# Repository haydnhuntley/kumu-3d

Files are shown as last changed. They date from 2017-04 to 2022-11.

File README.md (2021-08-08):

# kumu-3d

## The Kumu-3D Printer

### *Kumu* means *teacher* in the Hawaiian language.

I wish to thank Johann C. Rocholl for his groundbreaking work on the Rostock and Kossel 3D Printers. This design was derived from his work and that of many other innovators.

The Kumu-3D is a Delta printer improving on the [Kossel Plus](http://www.kosselplus.com "Kossel Plus"), which I designed to extend and improve on Johann's original [Kossel](http://reprap.org/wiki/Kossel "Kossel").

The Kumu-3D's features are:

* 300mm diameter borosilicate build plate, yielding a build area over 250mm in diameter.
* 250mm diameter 24V 250W silicone heater.
* 24v power supply, to give the motors twice as much power for faster acceleration and more precise positioning.
* E3D-style hotend.
* 32-bit Smoothieware controller from AZSMZ, with LCD display.
* Carbon fiber, magnetic, zero-backlash arms.
* 0.9&deg; motors, 1/32 stepping, 16-tooth pulleys yield 400 steps/mm with a worst case real world resolution of 20&micro;m and an average resolution of about one-third of that.
* Dampers for near silent operation.
* 2020 extrusions with diagonal bracing for increased stiffness.
* flying extruder for better retraction performance.
* optional 9mm GT2 belts for increased precision.
* Integrated spool holder with bearings on top.
* Build cost around $600 in quantity one, including US shipping.
* With the standard 750mm vertical extrusions and 304mm arms, it yields a maximum Z of 290mm and maximum diameter of 260mm.  With 1000mm vertical extrusions and 360mm arms, it should yield a build height of over 500mm and diameter up to 300mm.

Here is the GoogleDocs spreadsheet containing the [Bill of Materials](https://docs.google.com/spreadsheets/d/1ovnhxit7gjctnHXA3ArEihpogoxfmhG4zKcSKq6PfBs/edit?usp=sharing). 
Here is a list of the fasteners required and where they are used: [Fasteners](https://docs.google.com/spreadsheets/d/1ovnhxit7gjctnHXA3ArEihpogoxfmhG4zKcSKq6PfBs/edit#gid=828928504)

Note: this is no longer a *Work-in-Progress* -- nine Kumu-3D's have been built and are printing, and two more are on the way!  I'm in the process of writing up how to build them, which is at:  [Assembly Instructions](https://docs.google.com/document/d/1tWf-NENtzvH9kXuD4_r2AeAENZi3MvYkmVscPsnDQXc/edit?usp=sharing)

This isn't an average printer, it is an **extraordinary** one.

I've switched to using dual-drive, geared ("BMG" style) extruders. They have triple the torque, and double the filament grip.
I've been using $15 ones from DotBit, but there are many decent brands: https://www.aliexpress.com/item/4000419512195.html

Here is a link to the AZSMZ's LCD display holder (designed by Rick Yang):  [
LCD mount for AZSMZ 12864 with TF slot](http://www.thingiverse.com/thing:1610241)

Here are some photos of Kumu-3D#1:
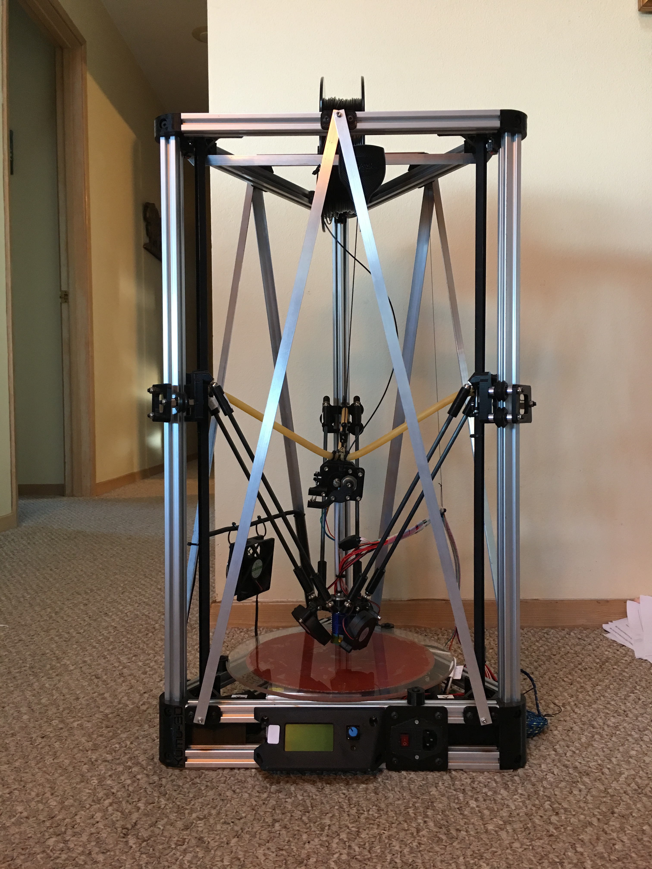
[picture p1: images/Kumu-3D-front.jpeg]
Kumu-3D Front Kumu-3D Front

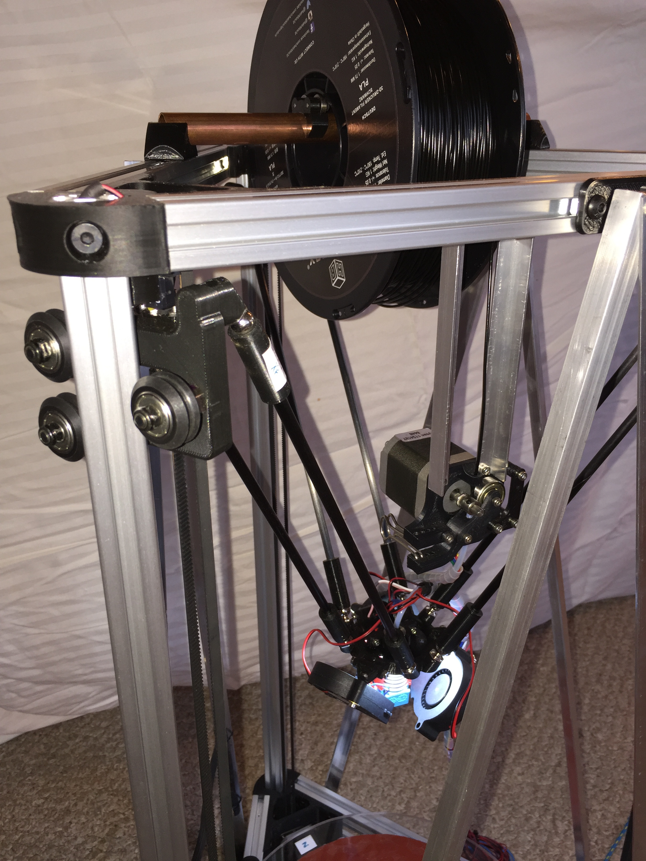
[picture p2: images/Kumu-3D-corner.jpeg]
Kumu-3D Corner Kumu-3D Corner

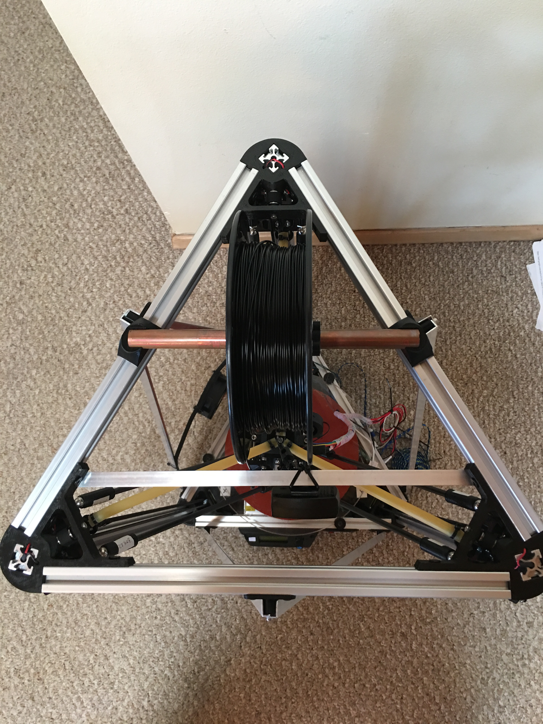
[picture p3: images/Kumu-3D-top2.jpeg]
Kumu-3D Top Kumu-3D Top

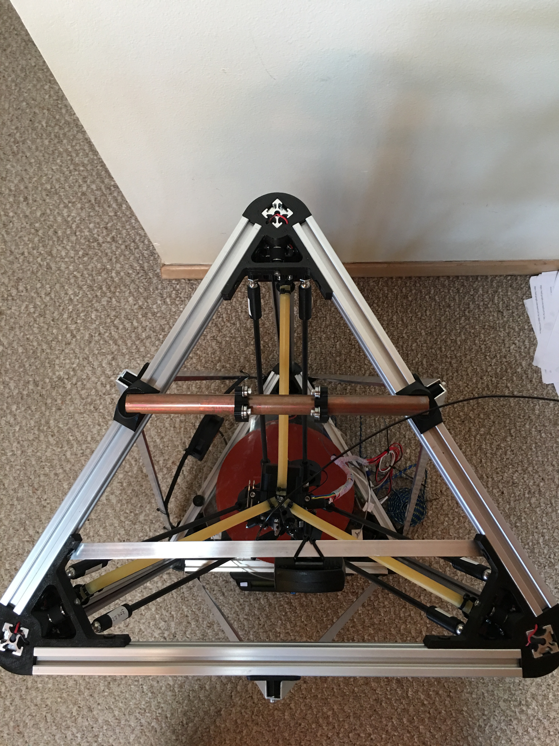
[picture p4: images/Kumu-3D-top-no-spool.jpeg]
Kumu-3D Top (no spool)


Here are some photos of a 3DBenchy torture test printed in PLA at 60mm/sec:
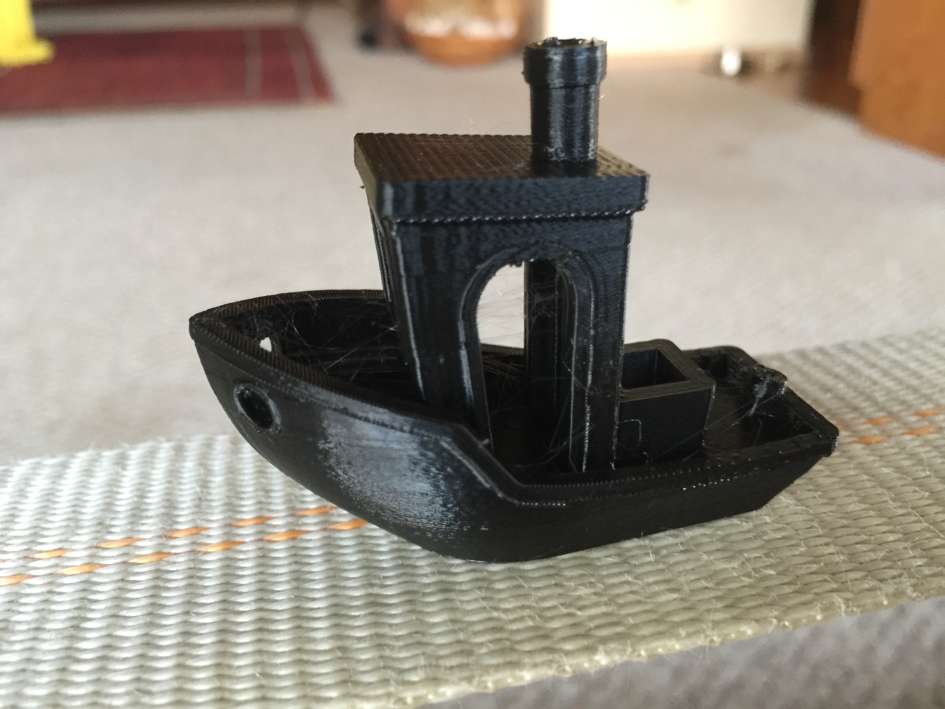
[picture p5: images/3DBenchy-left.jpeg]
3DBenchy Left 3DBenchy Left

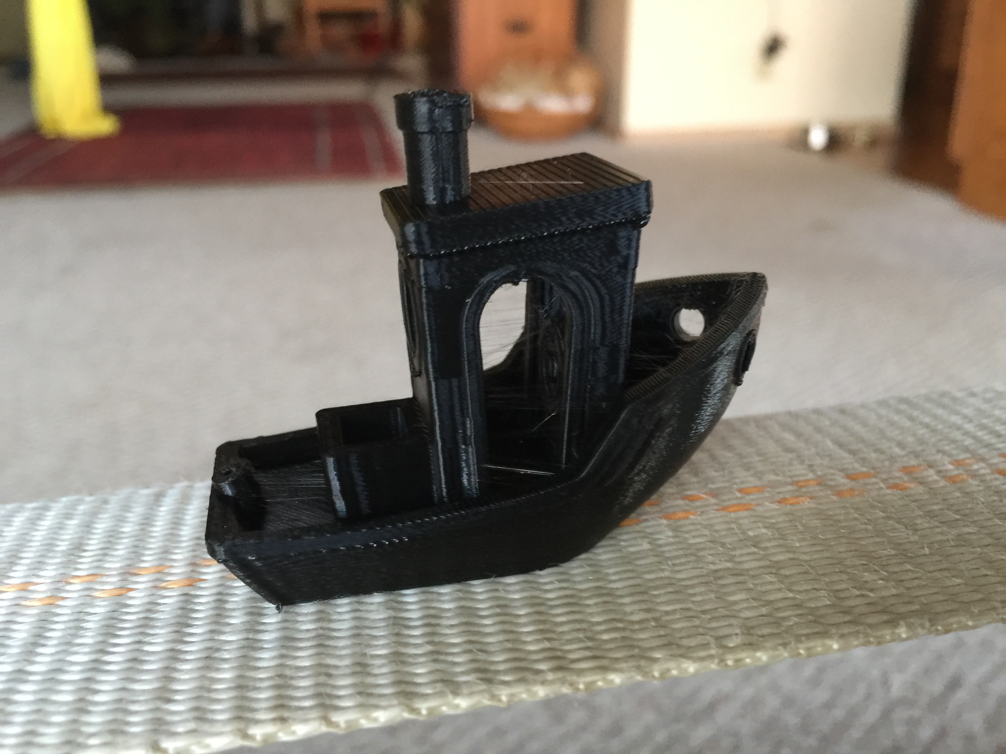
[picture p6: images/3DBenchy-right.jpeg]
3DBenchy Right

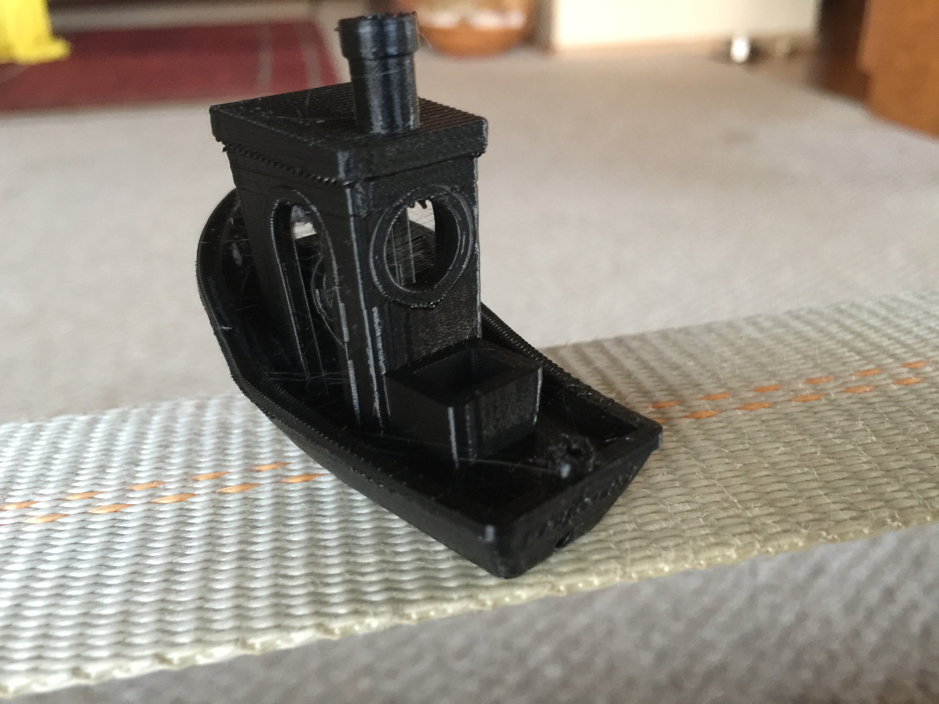
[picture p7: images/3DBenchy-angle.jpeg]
3DBenchy Angle

There is a little bit of very fine stringing, so I'll need to increase the retraction or lower the temperature.
(These were printed before switching to using the flying extruder.)
Note how nicely it handled the overhangs.

<!---
Some useful links for Markdown language:
 * [Adam's Markdown Cheatsheet](https://github.com/adam-p/markdown-here/wiki/Markdown-Cheatsheet)
 * [Laura's Markdown Cheatsheet](https://github.com/tchapi/markdown-cheatsheet/blob/master/README.md)
 * [Markdown Syntax Guide](https://confluence.atlassian.com/bitbucketserver/markdown-syntax-guide-776639995.html)
--->

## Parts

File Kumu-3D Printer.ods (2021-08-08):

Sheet: Non-printed parts
Cost | Quantity | Where Used | Description | Subtotal | Part Number | Source | Alternative Source
$20.00 | 1 | frame | 2020 aluminum extrusions | $20.00 | 2020KXL-Silver | http://www.robotdigg.com/product/494/2020-aluminum-extrusion-for-Kossel-XL
$7.64 | 3 | A-bracing, extruder mount | 8' pieces of 1/2" aluminum L-channel | $22.92 |  | http://www.homedepot.com/p/Everbilt-1-2-in-x-96-in-Aluminum-Angle-Bar-with-1-20-in-Thick-802677/204273980
$0.90 | 12 | carriages | eccentric spacers | $10.80 | PXZhu | http://www.robotdigg.com/product/626/Openbuilds-decentration-post
$1.49 | 6 | misc | packs of 10 M5x10 black steel low profile screws | $8.94 | 878 - pack | http://openbuildspartstore.com/low-profile-screws-m5/
$1.80 | 1 | misc | packs of 50 M5x8 black steel button head socket cap screws | $1.80 | BSCS-M5*8_50 | http://www.robotdigg.com/product/706/M3-or-M5-Button-Socket-Cap-Screw
$7.50 | 1 | misc | pack of 100 M5 pre-assembly T-nuts | $7.50 | PreNut20-M5 | http://www.robotdigg.com/product/317/Pre-assembly-T-nuts-for-2020-aluminum-profile
$84.00 | 1 | controller | AZSMZ 32bit controller, 12864 LCD, 5 x DRV8825 | $84.00 |  | http://www.ebay.com/itm/New-Ver-2-1-AZSMZ-32bit-controller-AZSMZ-12864-LCD-4-x-DRV8825-/262633912155
$6.75 | 1 | controller | 4GB or larger micro SD card | $6.75 |  | https://www.amazon.com/SanDisk-microSD-High-Capacity-microSDHC/dp/B00488G6P8
$9.00 | 1 | wiring | wiring harness | $9.00 |  | http://www.ebay.com/itm/171207706681
$21.96 | 1 | power | 24V 15A power supply | $21.96 |  | https://www.amazon.com/EAGWELL-Universal-Regulated-Switching-Computer/dp/B01IOK5FM0/
$1.00 | 1 | power | fuse holder/power switch/power cord socket | $1.00 | AC250-01A-Ear Screw Hole | http://www.robotdigg.com/product/744/AC-rocker-switch-power-inlet-socket-w/-fuse
$7.00 | 4 | stepper motors | NEMA17 0.9° stepper motors | $28.00 | 42HM48-1684 | https://www.robotdigg.com/product/1250/0.9-step-angle-NEMA17-stepper-motors
$2.20 | 3 | motor mounts | NEMA17 motor dampers | $6.60 | 17DAMPER | http://www.robotdigg.com/product/341/Antivibration-damper-4-nema17-stepper
$9.95 | 1 | hotend | E3D-style hotend, 24V, Bowden, 1.75mm | $9.95 | w/fan+PTFE tube, voltage: 24v, nozzle: 0.4mm/1.75mm | https://www.ebay.com/itm/All-Metal-Extruder-Hotend-Bowden-J-head-V6-For-Makerbot-Reprap-3D-printer-parts/132335314415 | https://www.filastruder.com/products/lite6?variant=1283850628
$14.99 | 1 | extruder | BMG-stle dual-drive, geared extruder | $14.99 |  | https://www.aliexpress.com/item/4000419512195.html
$5.00 | 1 | top corners (6), spool holder (4) | 10 pack of F623ZZ flanged bearings | $5.00 | F623ZZ | http://www.robotdigg.com/product/132/Flanged-Ball-Bearing-F623ZZ
$2.50 | 1 | top corners (3) | 10 pack of 623ZZ bearings | $2.50 | 623ZZ | https://www.robotdigg.com/product/62/623ZZ-Ball-Bearing
$0.60 | 1 | extruder | 608ZZ extruder bearing | $0.60 | S608ZZ | http://www.robotdigg.com/product/980/440C-SUS-Ball-Bearing-S608ZZ,-SF608ZZ
$1.80 | 12 | carriages | Delrin W-wheels | $21.60 | DelrinVSB | http://www.robotdigg.com/product/521/Delrin-or-SUS-Via-S-Bearing
$0.40 | 4 | limit switches | micro switches | $1.60 | SS-5GL0 | http://www.robotdigg.com/product/398/Pin-Plunger-Switch-Endstop
$20.99 | 1 | carriages | 5 meters of GT2 belt, 9mm wide | $20.99 |  | https://www.ebay.com/itm/GT2-2GT-open-Synchronous-Timing-Belt-Width-6-9-15mm-Small-Backlash-3D-Printer-/221884227725 | eBay: powge
$9.89 | 1 | carriages | pack of 5 GT2 16-tooth pulleys, 10mm wide, 5mm bore | $9.89 |  | https://www.ebay.com/itm/253544544720
$14.00 | 1 | bed | borosilicate glass bed, 300mm diameter, 5mm thick | $14.00 | Gls300-D300-5 Round | http://www.robotdigg.com/product/490/300mm-Borosilicate-Glass-for-3D-Printing
$18.00 | 1 | bed | silicone heater, 24v, 250mm diameter | $18.00 | SRht250-24VDC_Round | http://www.robotdigg.com/product/117/250mm-or-270mm-Silicone-Rubber-Heater-Pad
$113.00 | 1 | misc | RobotDigg.com express shipping | $113.00
$13.90 | 1 | tools | set of metric ball nose allen wrenches | $13.90 |  | https://www.amazon.com/gp/product/B0006O4ADI/
$39.95 | 1 | tools | 0-150mm calipers (optional but very useful) |  |  | https://www.amazon.com/Composite-Vernier-Digital-70019-Millimeters/dp/B01BEE86II
$2.97 | 1 | printing | glue stick, large (any brand is OK) | $2.97 |  | https://www.walmart.com/ip/Elmer-s-Large-School-Glue-Stick-22g-3pk/17011268
$22.98 | 1 | printing | kg of 1.75mm PLA filament | $22.98 |  | http://www.amazon.com/Hatchbox-1-75mm-3D-Printer-Filament/dp/B00J0ECR5I
 |  |  | Total | $475.29

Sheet: Fasteners
 | Counts | Upper Frame | Lower Frame | Vertical Extrusions | A-Bracing | Carriages | Effector | AZSMZ Holder | LCD Display Holder | Power Supply Holders | Fuse Plug Holder | Extruder | Flying Extruder Suspender | Copper Pipe Spool Holder | Copper Pipe Bearing Holder | Glass Holders
M5x50 | 12 |  |  |  |  | 12
M5x20 | 5 |  |  |  |  |  |  |  | 2 |  |  |  |  |  |  | 3
M5x10 | 54 | 12 | 24 | 18
M5x8 | 30 |  |  |  | 18 |  |  | 2 |  | 4 | 4 |  |  | 2
M5 pre-install nut | 89 | 12 | 24 | 18 | 18 |  |  | 2 | 2 | 4 | 4 |  |  | 2 |  | 3
M5 nylock nut | 12 |  |  |  |  | 12
M5 washer | 4 |  |  |  |  |  |  |  |  |  |  |  |  |  | 4
M3x35 | 9 |  |  |  |  | 9
M3x25 | 9 | 3 |  |  |  |  | 3 |  |  |  |  | 3
M3x20 | 8 |  |  |  |  |  | 5 |  |  |  |  | 1 | 2
M3x10 | 19 |  |  |  | 9 | 3 |  |  |  |  |  | 2 | 1 |  | 4
M3x8 | 12 |  | 6 |  |  |  |  | 4 |  |  |  | 2
M3x6 | 18 |  | 6 |  |  |  | 2 |  | 4 | 4 | 2
M3x4 | 2 |  |  |  |  |  |  |  |  |  | 2
M3 nut | 21 |  |  |  |  | 9 | 8 |  |  |  |  | 2 | 2
M3 nylock nut | 16 |  |  |  |  | 9 | 6 |  |  |  |  |  | 1
M3 washer | 10 | 3 |  |  |  |  | 3 |  |  | 4
M2.5x12 | 8 | 6 |  |  |  |  | 2

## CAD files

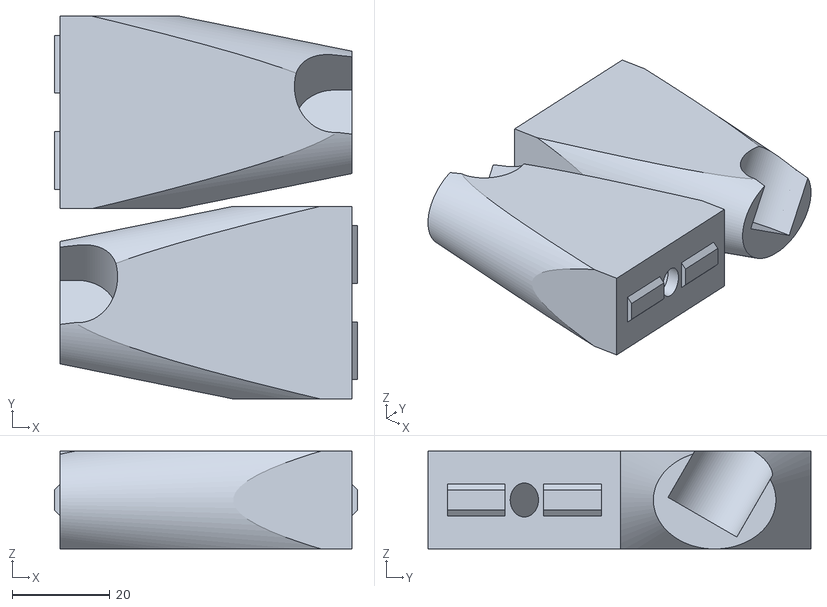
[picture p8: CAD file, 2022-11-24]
copperPipeSpoolHolder.stl
62.2 x 78.5 x 20.0

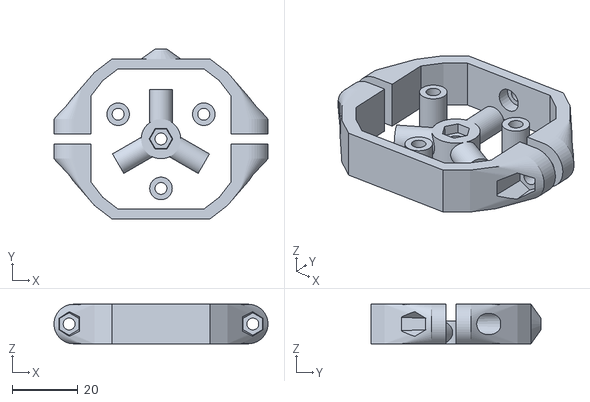
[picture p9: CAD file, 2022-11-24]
flyingExtruderSuspender.stl
64.9 x 51.5 x 12.0

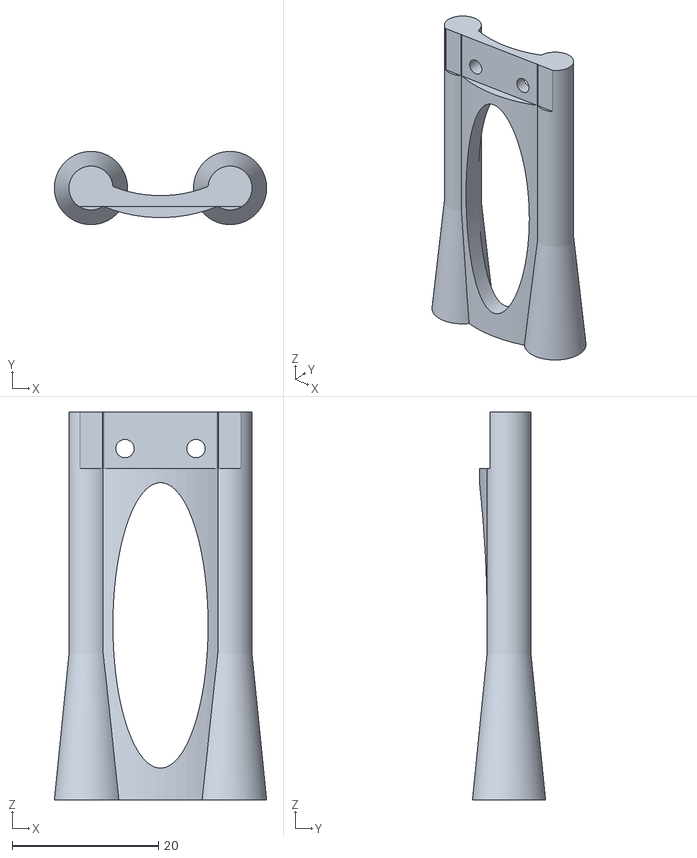
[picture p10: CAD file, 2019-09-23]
zProbe.stl
29.0 x 10.0 x 53.0

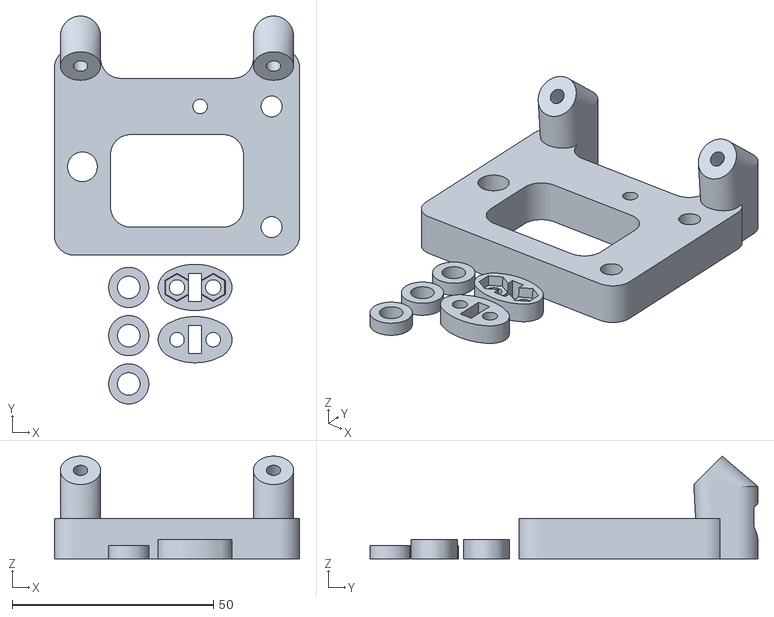
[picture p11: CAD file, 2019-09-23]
carriage.stl
61.0 x 96.5 x 25.6

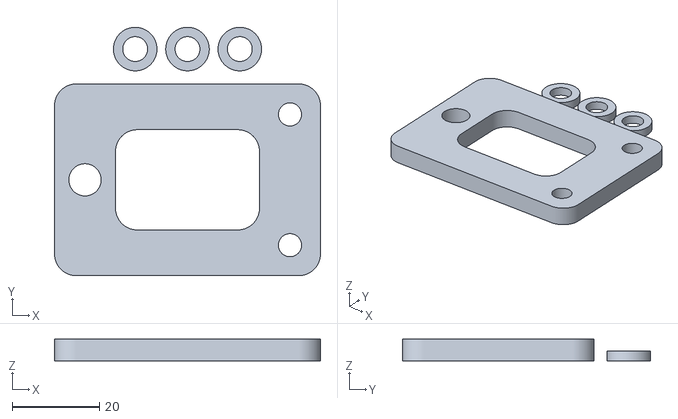
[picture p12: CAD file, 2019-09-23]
carriageOutside.stl
61.0 x 57.0 x 5.00

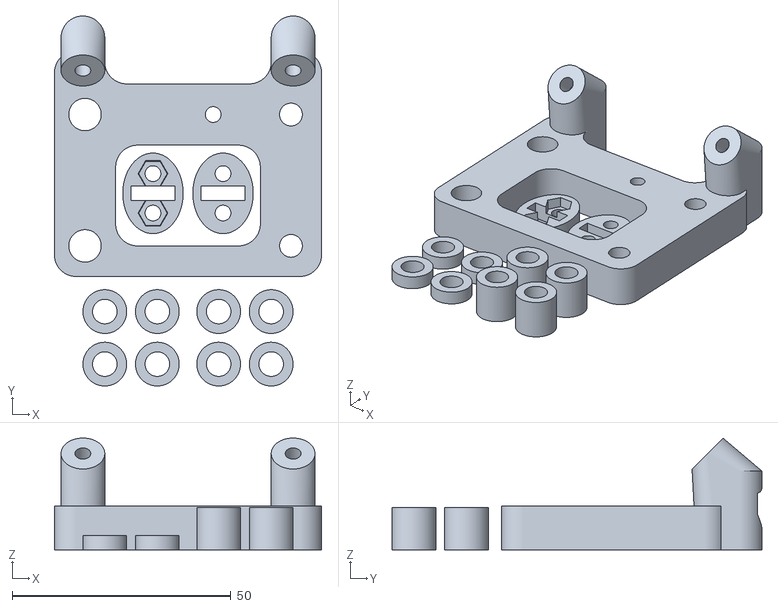
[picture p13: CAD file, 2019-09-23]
carriage4.stl
61.0 x 84.5 x 25.6

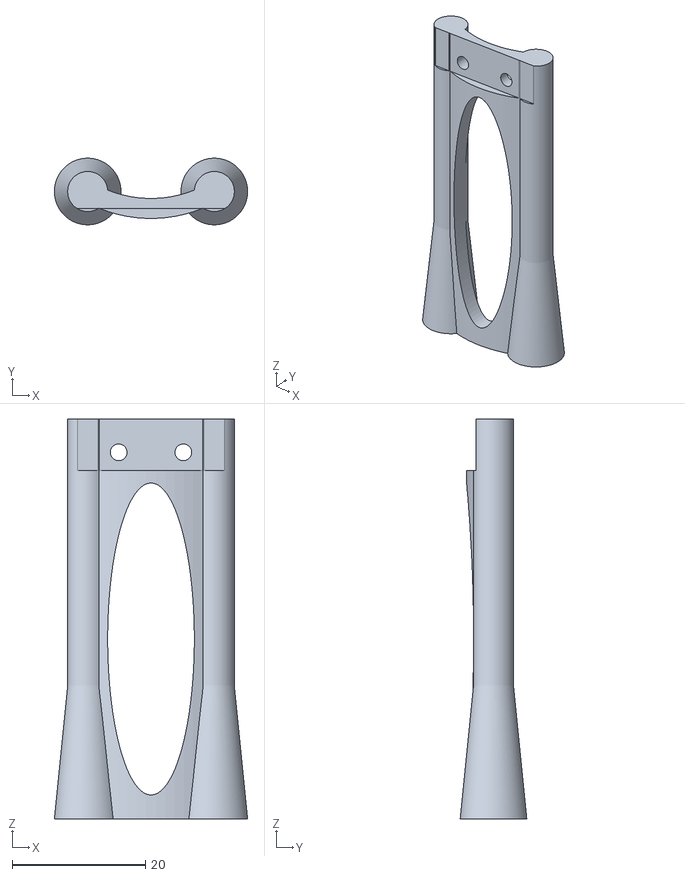
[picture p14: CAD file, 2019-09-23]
zProbeVolcano.stl
29.0 x 10.0 x 60.0

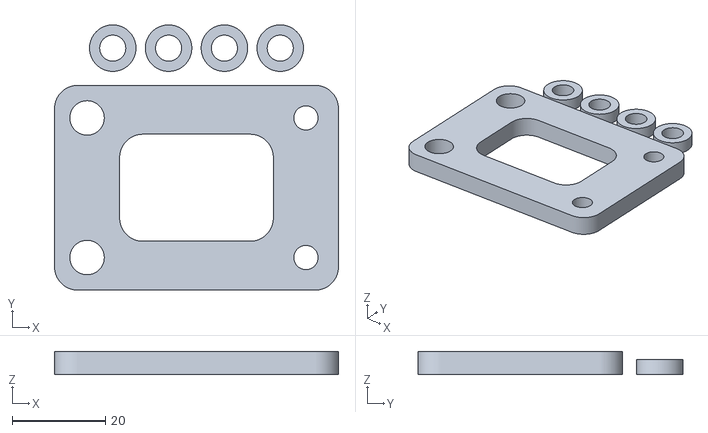
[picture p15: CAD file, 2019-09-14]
carriage4Outside.stl
61.0 x 57.0 x 5.00

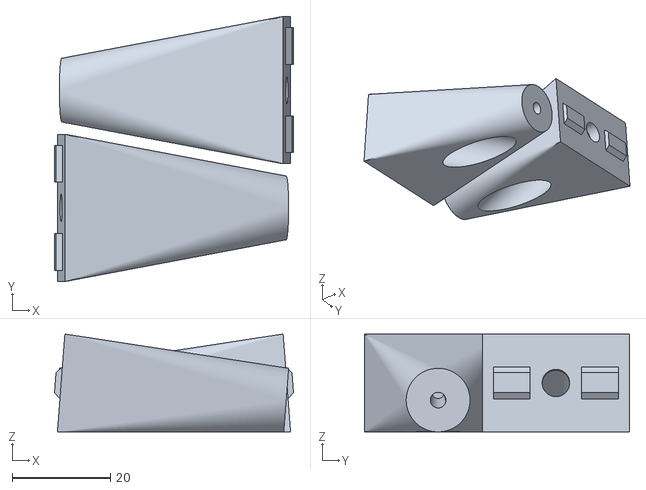
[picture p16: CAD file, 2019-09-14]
keyBakLifter.stl
48.7 x 54.0 x 19.9

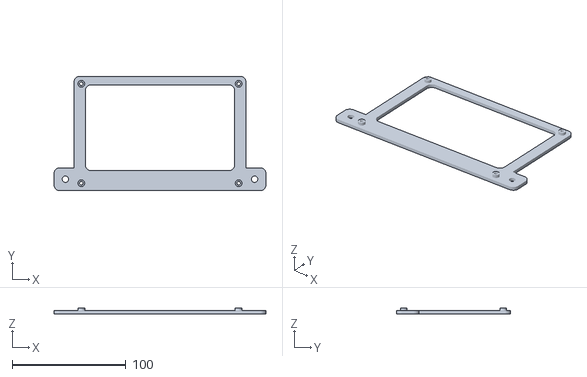
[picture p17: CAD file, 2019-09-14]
mksSbasePlate.stl
186.0 x 100.2 x 5.50

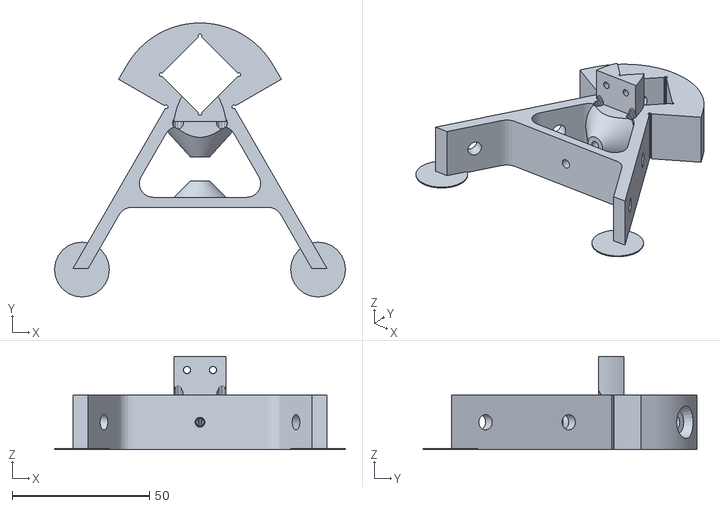
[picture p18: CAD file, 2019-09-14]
upperFrame.stl
106.0 x 99.8 x 34.0

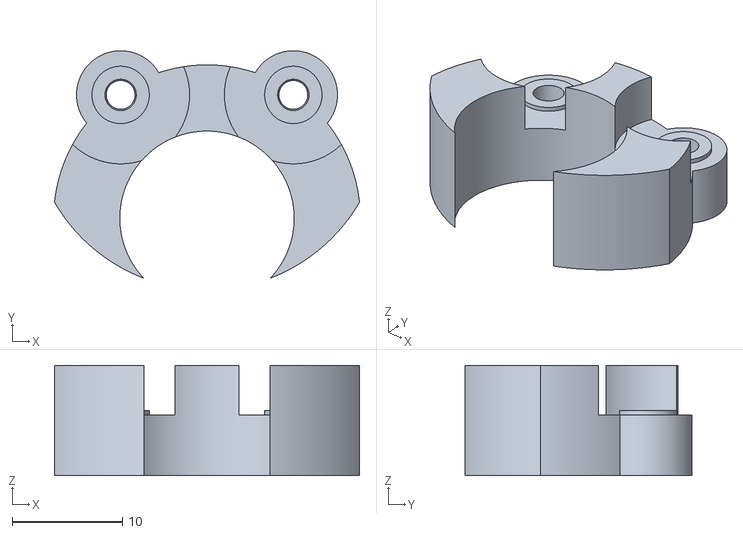
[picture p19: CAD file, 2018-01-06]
copperPipeBearingHolder.stl
27.6 x 20.6 x 10.0

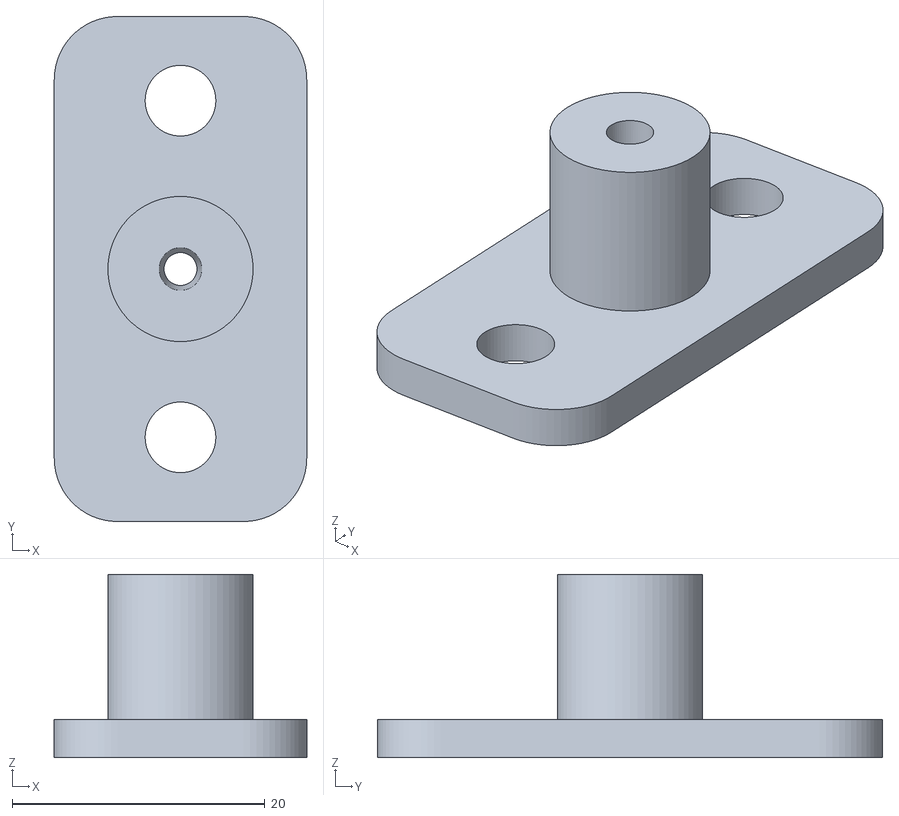
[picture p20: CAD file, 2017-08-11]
aBracingPost.stl
20.0 x 40.0 x 14.5

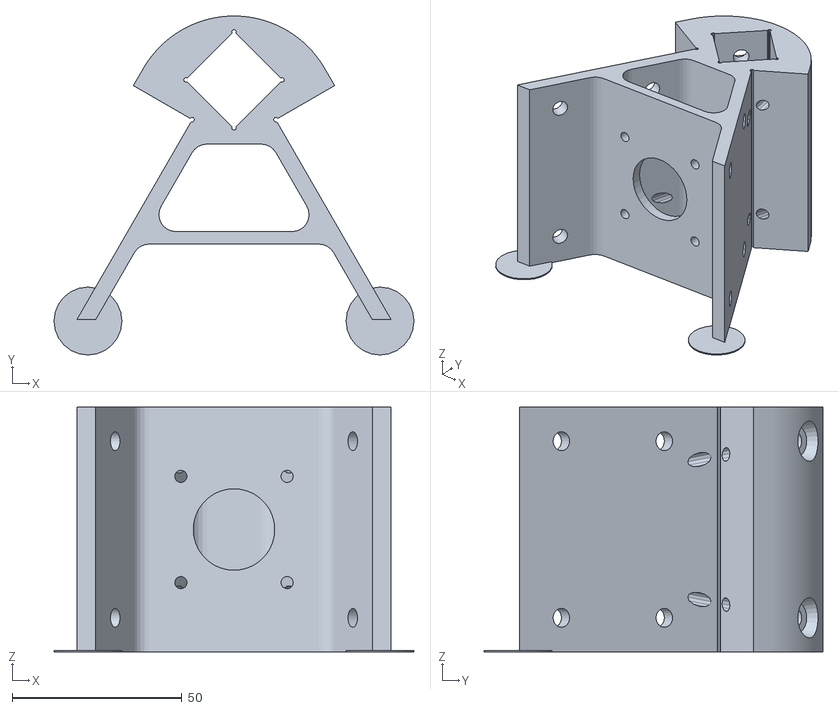
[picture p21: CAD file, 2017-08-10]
lowerFrame.stl
106.0 x 99.8 x 72.0

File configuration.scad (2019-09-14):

// Configuration file for the Kumu-3D printer.
//
// DO NOT SLICE THIS.
//
// This work is licensed under a Creative Commons Attribution-ShareAlike 4.0
// International License.
// Visit:  http://creativecommons.org/licenses/by-sa/4.0/
//
// Haydn Huntley
// haydn.huntley@gmail.com

// All measurements in mm.
smidge            = 0.1;
mmPerInch         = 25.4;
m3Radius          = (3.0 + 0.2) / 2;
m3LooseRadius     = m3Radius + 0.2;
m3TightRadius     = m3Radius - 0.2;
m3HeadHeight      = 3.0 + 0.2;
m3HeadRadius      = (5.4 + 0.2) / 2;
m3LooseHeadRadius = m3HeadRadius + 0.2;
m3NutRadius       = (6.25 + 0.75) / 2;
m3LooseNutRadius  = (m3NutRadius + 0.1);
m3TightNutRadius  = (m3NutRadius - 0.1);
m3NutHeight		  = 2.4;
m3NylockNutHeight = 4.0;
m3LooseNutHeight  = 2.4+0.2;
nozzleWidth		  = 0.5;
extrusionWidth    = 20.0;
copperPipeRadius  = 16.0/2 - smidge;
m5Radius          = (5.0 + 0.2) / 2;
m5LooseRadius     = m5Radius + 0.2;
m5TightRadius     = m5Radius - 0.2;
m5HeadHeight      = 5.6;		// For M5 SHCS
m5LooseHeadRadius = 8.6 / 2;	// For M5 SHCS
m5ButtonHeadRadius     = (9.5 + 0.3) / 2;  // For M5 button head
m5ButtonHeadHeight     = 2.5 + 0.5;
m5LowProfileHeadRadius = (9.5 + 0.3) / 2;  // For M5 low profile
m5LowProfileHeadHeight = 1.5 + 0.5;
m5x8Height        = 8;        // For M5x8
m5LooseNutRadius  = (8.9 + 0.4) / 2;
m5PlainNutHeight  = (3.8 + 0.2);
m5LockNutHeight   = (4.9 + 0.3);
m4LooseNutRadius  = (8.0 + 0.3) / 2;
m4NutHeight       = (3.2 + 0.3);

lowerFrameHeight    = 3 * extrusionWidth + 12;
ballJointSeparation = 48.0;

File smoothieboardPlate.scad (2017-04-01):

// Smoothieboard holder.
//
// This work is licensed under a Creative Commons Attribution-ShareAlike 4.0
// International License.
// Visit:  http://creativecommons.org/licenses/by-sa/4.0/
//
// Louis Dionne
// louis.dionne@gmail.com

$fn=360/6;

include <configuration.scad>;
include <roundedBox.scad>;

// All measurements in mm.
debug               = false;
xSize               = 129.6;
ySize				=  105;
zSize				=   3;
zPcBoard		    =   1.5;
pillarHeight		=   7 - zPcBoard;
edgeWidth           =  15;
outsideEdge         =   5;

// Smoothieboard holes.
upperLeft  = [      2.5, ySize-3];
upperRight = [xSize-28, ySize-3];
lowerLeft  = [     9, 8.5];
lowerRight = [xSize-28, 3.5];


module smoothieboardPlate()
{
	difference()
	{
		if (debug)
			translate([0, 0, pillarHeight])
			%cube([xSize, ySize, zPcBoard]);
	
		union()
		{
			// Make the body.
			translate([xSize/2, ySize/2, zSize/2])
			roundedBox([xSize+outsideEdge,
						ySize+outsideEdge,
						zSize], 5, true);

			// Add two tabs for M5x8 screws to attach to the aluminum
			// extrusions.
			translate([xSize/2, extrusionWidth/2-2.5, zSize/2])
			roundedBox([xSize+2*extrusionWidth,
						extrusionWidth,
						zSize],
					   5, true);
						
			// Add four pillars to elevate the PCB slightly.
			addPillar(upperLeft);
			addPillar(upperRight);
			addPillar(lowerLeft);
			addPillar(lowerRight);
		}

		// Make two M5x8 screw holes in the two tabs.
		translate([-extrusionWidth/2, extrusionWidth/2-2.5, 0])
		m5x8();
		translate([xSize+extrusionWidth/2, extrusionWidth/2-2.5, 0])
		m5x8();

		// Remove a cutout in the center.
		translate([xSize/2, ySize/2, zSize/2])
		translate([0, 5, 0])
		roundedBox([xSize-edgeWidth,
					ySize-edgeWidth - 8,
					zSize+smidge],
				   5, true);
				   
		// Make four M3x6 screw holes in the four pillars.
		m3x6(upperLeft);
		m3x6(upperRight);
		m3x6(lowerLeft);
		m3x6(lowerRight);
	}
}

module addPillar(pos)
{
	translate([pos[0], pos[1], 0])
	cylinder(r=m3LooseHeadRadius, h=pillarHeight);
}


module m3x6(pos)
{
	// These holes need to be slightly tight.
	translate([pos[0], pos[1], -smidge/2])
    cylinder(r1=m3Radius-smidge, r2=m3Radius, h=pillarHeight+smidge);
}


module m5x8()
{
	// These holes should be loose.
	translate([0, 0, -smidge/2])
	cylinder(r=m5LooseRadius, h=pillarHeight+smidge);
}


smoothieboardPlate();

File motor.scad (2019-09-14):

// A NEMA17 sized motor.
//
// DO NOT SLICE THIS.
//
// This work is licensed under a Creative Commons Attribution-ShareAlike 4.0
// International License.
// Visit:  http://creativecommons.org/licenses/by-sa/4.0/
//
// Haydn Huntley
// haydn.huntley@gmail.com


include <configuration.scad>;


nema17Width            = 42.5;
nema17Length           = 48;
nema17Diameter		   = 50;
nema17ShaftDiameter    =  5;
nema17ShaftLength      = 25;
nema17ShoulderDiameter = 22;
nema17ShoulderHeight   =  2;
nema17ScrewSpacing     = 31.3;
dampenerOffset         =  6;


module nema17Motor(motorLength=nema17Length)
{
	// Drawn with the shaft pointing toward the positive X-axis.
	
	// The motor's shaft.
	translate([motorLength/2, 0, 0])
	rotate([0, 90, 0])
	cylinder(r=nema17ShaftDiameter/2, h=nema17ShaftLength, $fn=24);

	// The motor's shoulder.
	translate([motorLength/2, 0, 0])
	rotate([0, 90, 0])
	cylinder(r=nema17ShoulderDiameter/2, h=nema17ShoulderHeight, $fn=24);
	
	// The rectangular body of the motor with rounded corners.
	intersection()
	{
		cube([motorLength, nema17Width, nema17Width], true);

		rotate([0, 90, 0])
		cylinder(r=nema17Diameter/2, h=motorLength, center=true, $fn=24);
	}
}

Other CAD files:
upperFrame9mm.stl
glassHolder.stl
azsmzPlate.stl
powerSupplyHolders.stl
aBracingPost.scad
Orbitron_Medium.scad
azsmzPlate.scad
carriage.scad
carriage4.scad
carriage4Outside.scad
carriageOutside.scad
copperPipeBearingHolder.scad
copperPipeSpoolHolder.scad
e3dWedge.scad
e3dWedge.stl
effector.scad
flyingExtruderSuspender.scad
fusePlugHolder.scad
fusePlugHolder.stl
glassHolder.scad
keyBakLifter.scad
lowerFrame.scad
mksSbasePlate.scad
powerSupplyHolders.scad
roundedBox.scad
smoothieboardPlate.stl
upperFrame.scad
upperFrame9mm.scad
vertex.scad
zProbe.scad
zProbeVolcano.scad

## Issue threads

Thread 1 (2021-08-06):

PDF / Word Dumps of Google Docs?

eduncan911, 2021-08-06:
Hello!  This is amazing and I am glad I found it before embarking on my up-sizing project of my 2020 Kossel !!

I've glanced over the Google Docs and will be using a number of techniques.  Thank you!

Question though: Could you download a copy of the Google Docs, and BOM, and include them in this repo for posterity?  That way, people can fork/download the repo and have a complete copy of all materials (such as I) in the event the repo and/or Google account goes offline.

I understand having them within Google Docs is easy to update to latest versions.  But hopefully, it's stable enough now to warranty a "version"?  :)

Thank you again!

haydnhuntley, 2021-08-08:
Hi Eric,

I added the BOM and Fasteners spreadsheet to the project.
I updated the project to reflect switching to using a BMG-style,
dual-drive, geared extruder.
I didn't add the instructions -- I haven't completed them.

I'm working on building a house with my partner, and at the moment we're
having sunny weather, so that's where most of my time/effort is going.

If you have any questions, just let me know, and I'll answer them ASAP!

--Haydn

Haydn Huntley
cell: 808-283-5173

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

eduncan911, 2021-08-08:
Thanks so much man!

haydnhuntley, 2021-08-08:
You bet!

:-)

--Haydn

Haydn Huntley
cell: 808-283-5173

On Sun, Aug 8, 2021 at 10:11 AM Eric Duncan ***@***.***>
wrote:

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

Closed 2021-08-08.

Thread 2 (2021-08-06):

Enable Discussions on the Repo?

eduncan911, 2021-08-06:
Github has a new feature called "Discussions" that allows people to post questions and accept answers, like Stackoverflow.

Could you enable it?  I have some general questions...  Though, I'll ask them here.  :)

1. What material did you print the upper and lower frames in?  ABS, PETG?  Or, is PLA stable enough?
2. I have a set of aluminum 2020 upper and lower frames from my existing Kossel.  Though, your versions looks very large and rigid.  Also, the aluminum versions are the wrong color scheme (hehe).  I'm wondering if you'd recommend the aluminum mounts over printed versions?
3. What is the "size limit" you think this 2020 version could scale up to?  I currently [have plans to go 1200mm on verticals, 470mm on horizontals, and 440mm mag rods](http://danalspub.com/DKcalc/?he=470&ve=1200&dr=440&lr=1000).  This would yield a build diameter of 400mm, and ~600mm heigh.

Everything else looks pretty good.  Great idea on the support braces.

haydnhuntley, 2021-08-07:
Hi Eric,

1)  I used PLA.  It has lasted for years!
2)  This printer uses 9mm belts, instead of the standard 6mm ones.  That
may be overkill, but I like making things strong and rigid.  It is my
understanding that the aluminum corners won't accommodate 9mm belts.
3)  I'd recommend using 9mm belts for a larger printer, and definitely
keeping the diagonal bracing.  I think you can go as big as you want, but
you may have to reduce acceleration if you notice the frame flexing.  I
don't notice any flexing on this size.

I've got a busy weekend, but I'll enable "discussions" in the next day or
so.

--Haydn

Haydn Huntley
cell: 808-283-5173

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

haydnhuntley, 2021-08-08:
"Discussions" are now enabled!  :-)

eduncan911, 2021-08-08:
Most excellent !!  I'll let you know if we have any more questions (two kids + me up-sizing it!!).  Will take a bit a curate the parts.

Closed 2021-08-08.

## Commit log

2017-02-27 Update README.md
    Updated the README and added links to the Kossel Plus, Kossel, and Bill of Materials.
2017-03-25 Initially committed the first parts.
    [Orbitron_Medium.scad, configuration.scad, copperPipeBearingHolder.scad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]
2017-03-25 Added the upper frame.
    [lowerFrame.scad, upperFrame.scad, upperFrame.stl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]
2017-03-26 Added microswitch holders and wiring tunnels.
    [upperFrame.scad, upperFrame.stl]
2017-03-26 Updated weight.
    [lowerFrame.scad]
2017-03-26 Added my locking E3D wedge.
    [e3dWedge.scad]
2017-03-26 Added the STL version of my E3D locking wedge.
    [e3dWedge.stl]
2017-03-26 Added glassHolder, improvements to upperFrame
    Enlarged the wiring tunnels and increased the gap for the idler bearings in the upperFrame.
    [glassHolder.scad, glassHolder.stl, lowerFrame.stl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]
2017-03-27 Added roundedBox.scad
    [roundedBox.scad]
2017-03-27 Added the AZSMZ holder.
    [azsmzPlate.scad, azsmzPlate.stl]
2017-03-27 Added the carriage.
    [carriage.scad, carriage.stl]
2017-03-28 Made the nut tunnels in lowerFrame more direct.
    [lowerFrame.scad, lowerFrame.stl]
2017-03-30 Added the pieces for implementing A-bracing.
    [aBracingPost.scad, aBracingPost.stl]
2017-04-01 Fixed a typo.
    [azsmzPlate.scad]
2017-04-01 Upper/lower frame modifications.
    Made lower frame 12mm taller to accommodate the fuse/plug/switch holder.
    Modified the upper/lower frame to use M5x10 bolts instead of M5x12 ones.
    Added license comments I noticed where they were missing.
    Added comments in motor.scad, roundedBox.scad, and vertex.scad to clarify that those shouldn't be sliced -- they're only included by other files.
    [configuration.scad, lowerFrame.scad, lowerFrame.stl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]
2017-04-01 Added the fuse/plug/switch holder.
    [fusePlugHolder.scad, fusePlugHolder.stl]
2017-04-01 Added plates for Smoothieboard and MKS SBASE.
    Both contributed by Louis Dionne.
    [mksSbasePlate.scad, mksSbasePlate.stl, smoothieboardPlate.scad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]
2017-04-01 Made some of the M3 holes a little tighter.
    Also corrected some comments.
    [azsmzPlate.scad, azsmzPlate.stl, mksSbasePlate.scad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]
2017-04-02 Fixed a bug in the upperFrame.
    I accidentally introduced it with my previous commit.
    [upperFrame.scad, upperFrame.stl]
2017-04-02 Fixed a typo in a comment.
    [mksSbasePlate.scad]
2017-04-14 Fixed nut traps.
    The nut traps were tapering the wrong direction, and they weren't deep enough.
    Also made the hole for the eccentric spacer a little tighter.
    [carriage.scad, carriage.stl]
2017-04-14 thinner spacers.
    Thinner spacers (by 2mm) and slightly stronger ball stud nut traps.
    Slightly smaller hole for eccentric spacer.
    [carriage.scad, carriage.stl]
2017-04-14 Shortened spacers.
    This allowed a switch from M5x40 to M5x35 bolts.
    Also tightened the holes for the eccentric spacers.
    [carriage.scad, carriage.stl]
2017-04-15 Corrected printed weight.
    [lowerFrame.scad]
2017-04-15 Added power supply holders.
    [powerSupplyHolders.scad, powerSupplyHolders.stl]
2017-04-15 Updated a comment.
    [copperPipeBearingHolder.scad]
2017-04-15 Made keyway thinner for RobotDigg extrusions.
    [copperPipeSpoolHolder.scad, copperPipeSpoolHolder.stl]
2017-04-15 Modified it for M5x12 -> M5x15
    [glassHolder.scad, glassHolder.stl]
2017-04-23 Modified AZSMZ holder to accommodate capacitor.
    There was a capacitor which wouldn't fit, necessitating this redesign.
    [azsmzPlate.scad, azsmzPlate.stl]
2017-04-23 Finished testing the printed parts.
2017-05-14 Added 5mm more room for silicone bed heater.
    It was bumping into the power supply.
    [glassHolder.scad, glassHolder.stl]
2017-08-10 Modified the vertex.
    Modified the vertex to slightly flare the bottom of the opening for the vertical extrusion to compensate for the way the first layer tends to squish and make it too tight.
    [lowerFrame.stl, upperFrame.scad, upperFrame.stl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]
2017-08-10 Added versions for 9mm belts.
    9mm belts are a little more than 50% stronger/stiffer than 6mm ones. These parts work with 9mm belts.
    [beltLocks9mm.scad, beltLocks9mm.stl, upperFrame9mm.scad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]
2017-08-10 Added outside carriage pieces.
    These make the carriages substantially stiffer.
    [carriageOutside.scad, carriageOutside.stl]
2017-08-11 Modified the M3 hole to make it larger.
    It was too small.
    [aBracingPost.scad, aBracingPost.stl]
2017-10-31 Added m3 nylock nut height and m4 measurements.
    [configuration.scad]
2017-10-31 Initially added it.
    [flyingExtruderSuspender.scad, flyingExtruderSuspender.stl]
2017-10-31 Added flying extruder and 9mm belts.
2017-11-09 Improved nut traps.
    [beltLocks9mm.scad, beltLocks9mm.stl]
2017-11-09 Improved nut traps, thickened spacers.
    Also, corrected M5 lengths for axles.
    The thicker spacers give better clearance.
    [carriage.scad, carriage.stl, carriageOutside.scad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]
2017-11-23 Added post-flying extruder suspender images.
2017-11-23 With flying extruder.
2017-11-23 Removed the top mounted extruder version.
2018-01-06 Added m3TightRadius.
    [configuration.scad]
2018-01-06 Now uses slightly smaller, tapered M3 holes.
    [copperPipeBearingHolder.scad, copperPipeBearingHolder.stl]
2018-03-10 Added ballJointSeparation.
    [configuration.scad]
2019-09-14 Made the horizontal M3 hole slightly more tapered to grip better.
    [upperFrame.scad, upperFrame.stl]
2019-09-14 Renamed constants.
    [motor.scad]
2019-09-14 Minor changes.
    [mksSbasePlate.stl]
2019-09-14 Added Key-Bak lifter to help support flying extruder.
    [keyBakLifter.scad, keyBakLifter.stl]
2019-09-14 Strengthened it a bit.
    I had two break after a year.
    This has solved the problem.
    [flyingExtruderSuspender.scad, flyingExtruderSuspender.stl]
2019-09-14 Made them taller, to avoid bumping into flying extruder.
    [copperPipeSpoolHolder.scad, copperPipeSpoolHolder.stl]
2019-09-14 Removed some unused definitions, and added m5NutHeight.
    [configuration.scad]
2019-09-14 Initially committed the effector for E3D type hotends.
    [effector.scad]
2019-09-14 The better, more stable 4-wheeled carriage parts.
    [carriage4.scad, carriage4.stl, carriage4Outside.scad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]
2019-09-23 Added the z-probe for calibrating.
    This one works with an E3-style hotend.
    [zProbe.scad, zProbe.stl]
2019-09-23 z-probe for a Volcano hotend.
    [zProbeVolcano.scad, zProbeVolcano.stl]
2019-09-23 The 9mm belt locks are the default in carriage4.
    [beltLocks9mm.scad]
2019-09-23 Uploaded the latest versions.
    [carriage.stl, carriage4.stl, carriageOutside.stl]
2019-09-23 Corrected the rights message.
    [zProbe.scad, zProbe.stl]
2019-09-23 Removed some unnecessary holes.
    They were for Tim Jacobsen's "strings and springs" method, but they tended to deform this effector, so I'm no longer testing them.
    [effector.scad]
2021-08-08 Added spreadsheet with bill of materials and list of fasteners.
    [Kumu-3D Printer.ods]
2021-08-08 Updated to reflect switch to using DotBit dual-drive extruder.
2021-08-08 Switched to DotBit dual-drive, geared extruder.
    [Kumu-3D Printer.ods]
2022-11-24 Modified it to make it thicker.
    I had a 10mm thick one break, so now it is 12mm thick.
    [flyingExtruderSuspender.scad, flyingExtruderSuspender.stl]
2022-11-24 Reoriented the parts, to print more compactly.
    [copperPipeSpoolHolder.scad, copperPipeSpoolHolder.stl]
